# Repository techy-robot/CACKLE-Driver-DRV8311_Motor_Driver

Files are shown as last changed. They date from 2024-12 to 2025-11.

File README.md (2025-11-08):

---
modified: 2025-11-07T22:07:04-07:00
---

# DRV8311 Motor Driver

> [!TIP]
> This board is part of a larger modular control board ecosystem, [CACKLE](https://github.com/techy-robot/CACKLE)

This is a single brushless motor driver based on the DRV8311 Texas Instruments chip. It is capable of 5 amps current in a voltage range of 3 to 24 volts. It has integrated current sense amplifiers and protection logic. It supports up to 200khz PWM frequency.

The chip has 3 current sense outputs, tied to all three ADC pins. The motor output is through a Molex Picoblade (1.25mm pitch) 3-pin connector.

The module is a 4-layer PCB with additional exposed traces for the power and ground to add solder for more current carrying capability. I designed it to carry 10 amps with 1 oz outer copper and 0.5oz inner copper, which can be increased to 20 amps current by adding solder. This was the cheapest method to go with, since 2 oz copper would add an additional 30$ per 5 boards. 

Schematic PDF

3D model
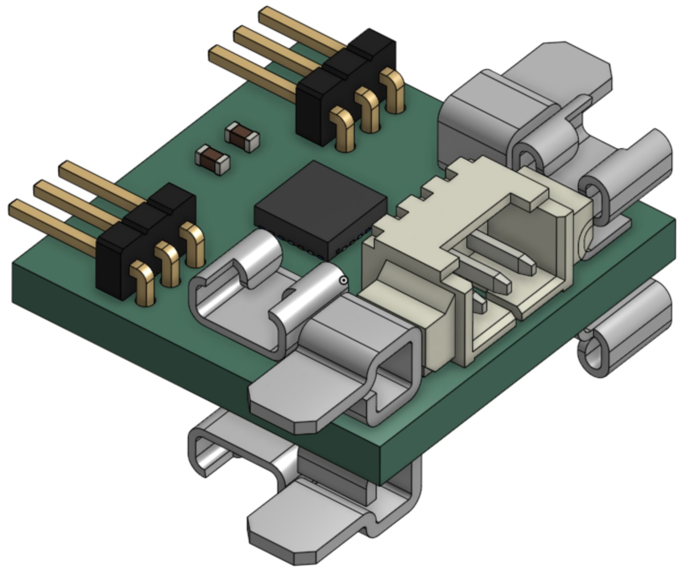
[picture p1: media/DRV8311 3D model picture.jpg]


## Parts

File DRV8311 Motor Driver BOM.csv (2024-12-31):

Id | Designator | Footprint | Quantity | Designation | Supplier and ref
1 | J7,J9,J3,J11 | Keystone_3579 | 4 | Keystone 3579
2 | J4 | Molex_PicoBlade_53048-0310_1x03_P1.25mm_Horizontal | 1 | Molex Picoblade
3 | C1 | C_0402_1005Metric | 1 | 4.7uF, 10v
4 | U1 | DRV8311_0.3mmVias | 1 | DRV8311HRRWR
5 | J8,J6,J10,J5 | Keystone_3569_half | 4 | Keystone 3569
6 | C6,C2 | C_0603_1608Metric | 2 | 100nF, 16v
7 | J2,J1 | PinHeader_1x03_P1.27mm_Horizontal | 2 | 1.27mm pin header
8 | C7,C3 | C_0402_1005Metric | 2 | 100nF, 16v
9 | R1 | R_0402_1005Metric | 1 | 300k
10 | C4,C9,C10,C8,C5 | C_0603_1608Metric | 5 | 10uF, 16v
11 | R3 | R_0402_1005Metric | 1 | 47k
12 | R2 | R_0402_1005Metric | 1 | 100k

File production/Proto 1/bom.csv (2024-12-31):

Designator | Footprint | Quantity | Value | LCSC Part #
C1 | 0402 | 1 | 4.7uF, 10v | C23733
C10, C4, C5, C8, C9 | 0603 | 5 | 10uF, 16v | C96446
C2, C6 | 0603 | 2 | 100nF, 16v | C14663
C3, C7 | 0402 | 2 | 100nF, 16v | C1525
J4 | Molex_PicoBlade_53048-0310_1x03_P1.25mm_Horizontal | 1 | Molex Picoblade | C505275
R1 | 0402 | 1 | 300k | C25774
R2 | 0402 | 1 | 100k | C25741
R3 | 0402 | 1 | 47k | C25792
U1 | DRV8311_0.3mmVias | 1 | DRV8311HRRWR | C5218862

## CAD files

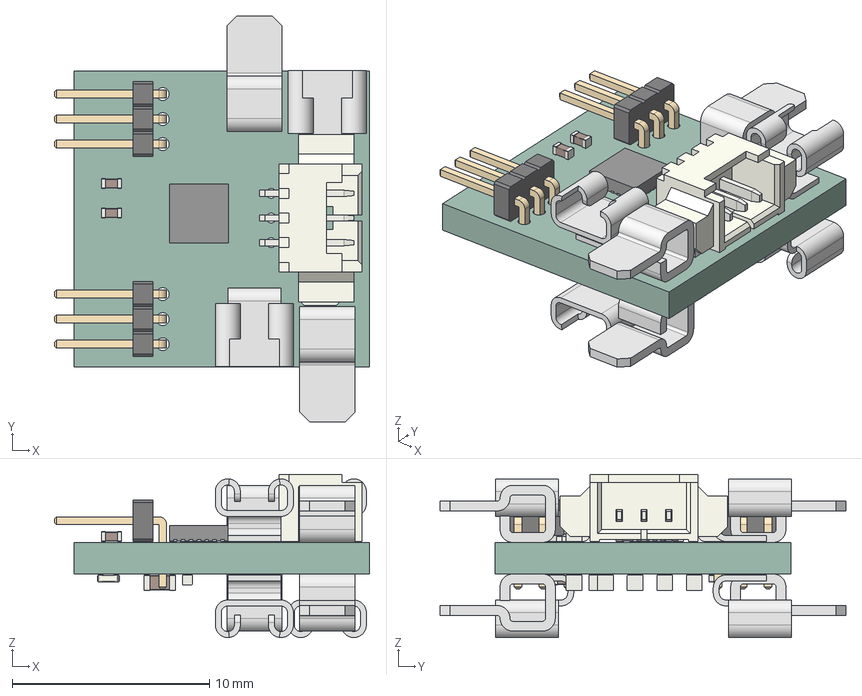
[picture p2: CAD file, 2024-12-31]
DRV8311 Motor Driver.step
16.0 x 20.6 x 8.28 mm
Keystone 3579 x 4
Molex_53261_0371
C_0402_1005Metric x 3
RRW0024A_ASM
Keystone 3569 half x 4
C_0603_1608Metric x 7
PinHeader_1x03_P127mm_Horizontal x 2
R_0402_1005Metric x 3
DRV8311 Motor Driver_PCB

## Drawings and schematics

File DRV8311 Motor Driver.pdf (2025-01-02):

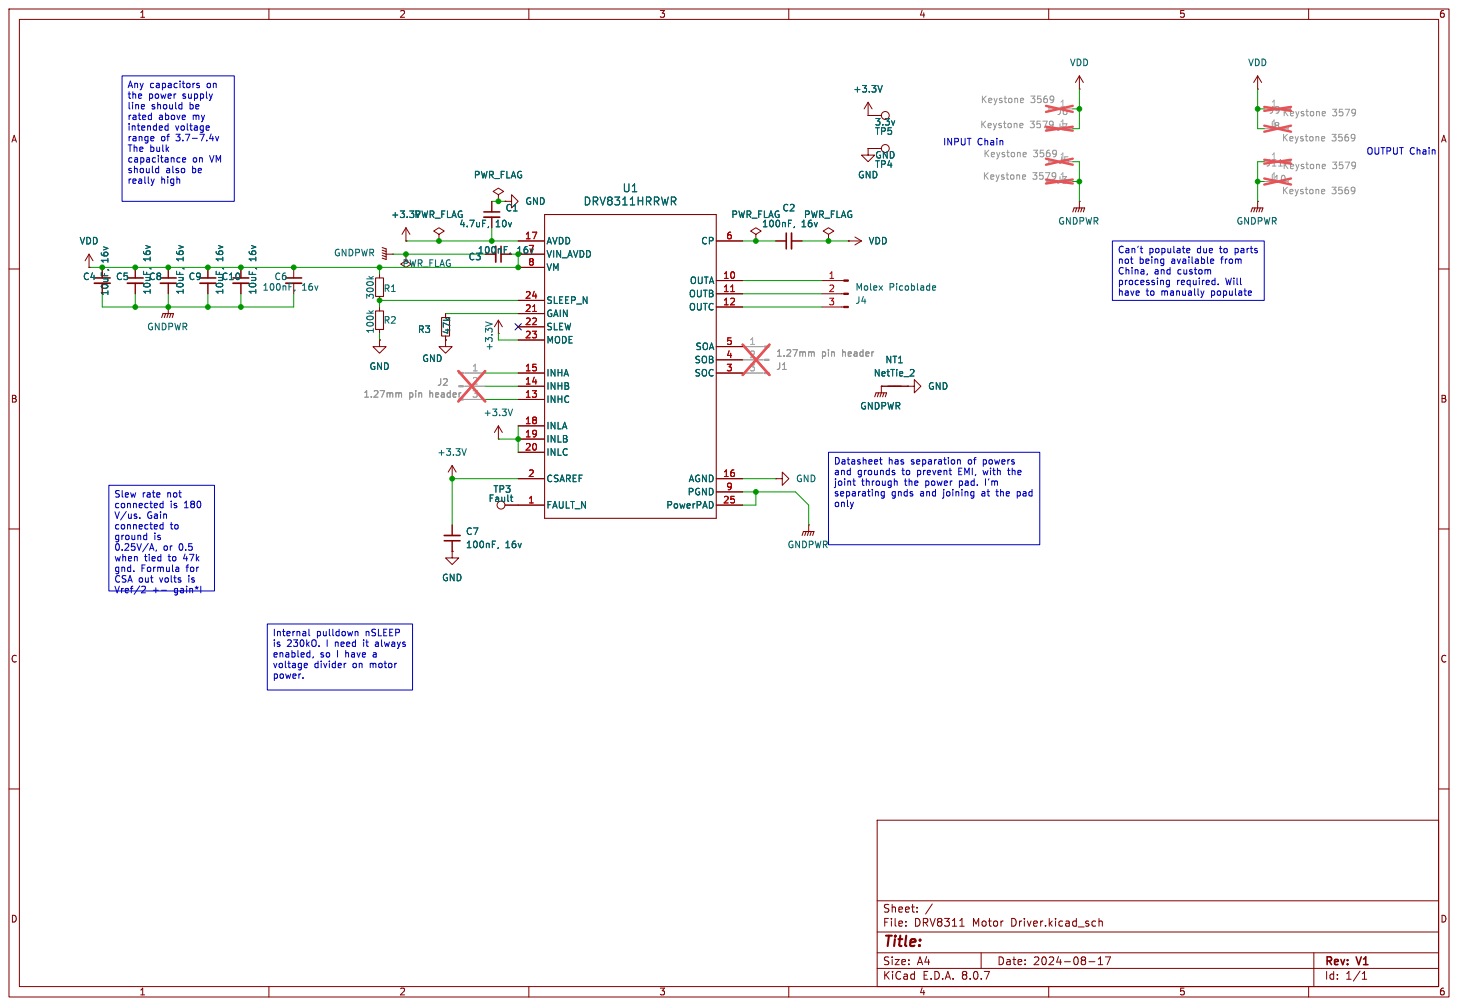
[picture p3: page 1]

the power supply
line should be
rated above my
range of 3.7-7.4v The bulk

joint through the power pad. I'm
only

is 230kO. I need it always enabled, so I have a

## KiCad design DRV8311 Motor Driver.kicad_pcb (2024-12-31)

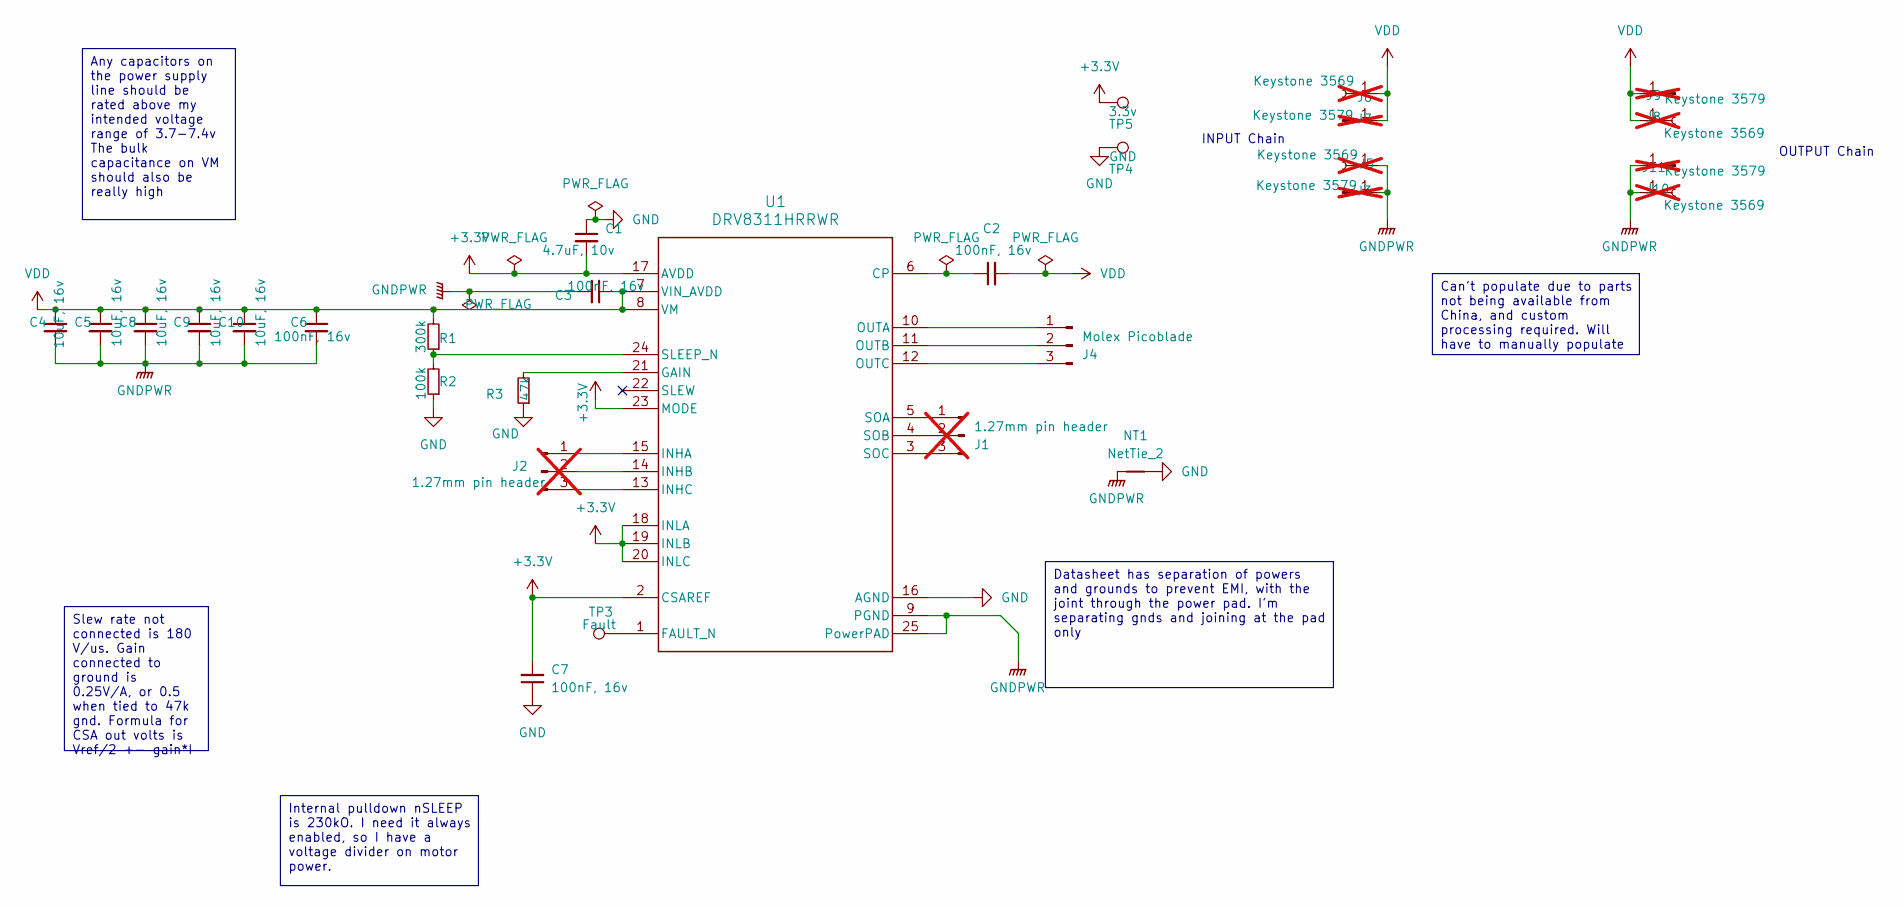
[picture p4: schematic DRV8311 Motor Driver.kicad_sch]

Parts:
C1: 4.7uF, 10v; C_0402_1005Metric
C2, C6: 100nF, 16v; C_0603_1608Metric
C3, C7: 100nF, 16v; C_0402_1005Metric
C4, C5, C8, C9, C10: 10uF, 16v; C_0603_1608Metric
J1, J2: 1.27mm pin header; PinHeader_1x03_P1.27mm_Horizontal; not fitted
J3, J7, J9, J11: Keystone 3579; Keystone_3579; not fitted
J4: Molex Picoblade; Molex_PicoBlade_53048-0310_1x03_P1.25mm_Horizontal
J5, J6, J8, J10: Keystone 3569; Keystone_3569_half; not fitted
NT1: NetTie_2; NetTie-2_SMD_Pad0.2mm
R1: 300k; R_0402_1005Metric
R2: 100k; R_0402_1005Metric
R3: 47k; R_0402_1005Metric
TP3: Fault; TestPoint_Pad_D1.0mm
TP4: GND; TestPoint_Pad_D1.0mm
TP5: 3.3v; TestPoint_Pad_D1.0mm
U1: DRV8311HRRWR; DRV8311_0.3mmVias

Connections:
+3.3V: C1.2, C7.2, TP5.1, U1.2 (CSAREF), U1.17 (AVDD), U1.18 (INLA), U1.19 (INLB), U1.20 (INLC), U1.23 (MODE)
GND: C1.1, C7.1, NT1.2, R2.1, R3.1, TP4.1, U1.16 (AGND)
GNDPWR: C3.2, C4.2, C5.2, C6.2, C8.2, C9.2, C10.2, J3.1, J5.1, J10.1, J11.1, NT1.1, U1.9 (PGND), U1.25 (PowerPAD)
unnamed: J1.1, U1.5 (SOA)
unnamed: J1.2, U1.4 (SOB)
unnamed: J1.3, U1.3 (SOC)
unnamed: J2.1, U1.15 (INHA)
unnamed: J2.2, U1.14 (INHB)
unnamed: J2.3, U1.13 (INHC)
unnamed: J4.1, U1.10 (OUTA)
unnamed: J4.2, U1.11 (OUTB)
unnamed: J4.3, U1.12 (OUTC)
unnamed: C2.1, U1.6 (CP)
unnamed: TP3.1, U1.1 (FAULT_N)
unnamed: R3.2, U1.21 (GAIN)
unnamed: R1.1, R2.2, U1.24 (SLEEP_N)
VDD: C2.2, C3.1, C4.1, C5.1, C6.1, C8.1, C9.1, C10.1, J6.1, J7.1, J8.1, J9.1, R1.2, U1.7 (VIN_AVDD), U1.8 (VM)

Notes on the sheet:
Internal pulldown nSLEEP is 230kO. I need it always enabled, so I have a voltage divider on motor power.
Can't populate due to parts not being available from China, and custom processing required. Will have to manually populate
Slew rate not connected is 180 V/us. Gain connected to ground is 0.25V/A, or 0.5 when tied to 47k gnd. Formula for CSA out volts is Vref/2 +- gain*I
Datasheet has separation of powers and grounds to prevent EMI, with the joint through the power pad. I'm separating gnds and joining at the pad only
Any capacitors on the power supply line should be rated above my intended voltage range of 3.7-7.4v The bulk capacitance on VM should also be really high
INPUT Chain
OUTPUT Chain

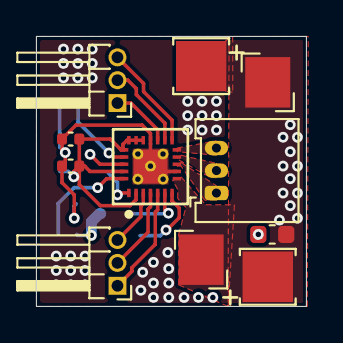
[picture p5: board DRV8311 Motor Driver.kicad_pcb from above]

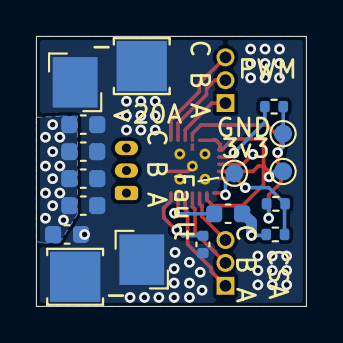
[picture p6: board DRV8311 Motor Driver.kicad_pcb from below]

Board: 4 copper layers, 15.0 x 15.0 mm, 29 parts (17 on the bottom side), 17 nets.

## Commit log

2024-12-31 Rearranged design files
    Instead of "Kicad" the main design folder is now named "Hardware" since I have gerbers and notes besides the kicad files. I have also put my designs in their proper categories.
    [DRV8311 Motor Driver BOM.csv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]
2025-01-02 Added schematic PDFs for all boards
2025-01-04 Added gerber zip files
2025-01-13 Changed link names for schematic embeds not displayin
    In Obsidian I can see the pdf embeds perfectly fine, but Github doesn't want to show embedded PDFs. I changed the link alias to "Schematic PDF" so people know what the link is when it doesn't display
2025-10-10 Moved all current production files to Proto 1.
    I haven't made a 2nd prototype yet
    [DRV8311 Motor Driver-B_Cu.gbl, DRV8311 Motor Driver-B_Mask.gbs, DRV8311 Motor Driver-B_Paste.gbp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]

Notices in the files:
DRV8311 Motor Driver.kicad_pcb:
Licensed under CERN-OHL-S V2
